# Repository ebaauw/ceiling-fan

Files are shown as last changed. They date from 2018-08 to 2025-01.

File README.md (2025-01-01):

# ceiling-fan

## Ceiling Fan control from deCONZ
Copyright © 2018-2025 Erik Baauw. All rights reserved.

This repository documents my efforts for controlling my dumb ceiling fans from [deCONZ](https://github.com/dresden-elektronik/deconz-rest-plugin), and, through [homebridge](https://github.com/nfarina/homebridge) and [homebridge-hue](https://github.com/ebaauw/homebridge-hue), from HomeKit.
As no-one seems to have done this before (see [deCONZ issue #717](https://github.com/dresden-elektronik/deconz-rest-plugin/issues/717)), I decided to try and hack together my own solution.

I have three regular ceiling fans.  Each fan has a single-phase 240V, 50Hz AC motor, and three GU.10 light spots.  As I've already installed smart lights, I'm only looking for a solution to smartify the control the fan speed, and possibly the direction.

The fan has four connection wires under the canopy: Motor Life (black), Lights Life (also black), Neutral (blue) and Ground (green/yellow).  My ceiling outlet only has three wires: Life (black, from the traditional wall switch) Neutral (blue), Earth (green/yellow), so the motor and lights are controlled by a single wall switch wire.  The smart lights prefer to be powered on always, so the wall switch is used only to cut power from the fan, not for regular control.  As I don't want to pull a new switched life wire, replacing the wall switch is not an option.

### ZigBee In-Wall Switch
My first attempt was to try and install a ZigBee in-wall switch in the fan's canopy, in between the incoming life wire and the motor life wire.  I mutilated an Xiaomi Aqara in-wall switch (`lumi.ctrl_ln2.aq1`), took off the front and cut off the edges supporting the keys, leaving a 6cm by 6cm by 3cm box, which fits the canopy.  After assembling the fan, it worked.  No speed control, but deCONZ was able to switch the fan on and off at speed preset by the pull-chain switch.

However, the Xiaomi switch broke while I was balancing the fan's blades (frequently switching on and off the fan using the Xiaomi switch).  The relays switch off automatically a second after switching on, or won't switch on at all.  Not sure if this is just my luck, or whether the switch doesn't like the fan starting up.  The fan is 50W, while the switch is rated for 2500W (10A).  Incidentally, one of my OSRAM Lightify smart plugs (the old model) exhibits the same symptoms.  It was powering a portable fan...

Before the switch broke, I already ordered two more Xiaomi switches.  They turned out to be the newer ones without a Neutral connection (they use a minute current on the one of the L1 or L2 wires to power the electronics).  That means they're powered off, when the pull-chain is in the off position.   Also, these are the end-device variants (`lumi.ctrl_neutral2`), now fully supported in deCONZ v2.05.37.  I mutilated the housing and installed them, fingers crossed.

#### Update after Several Months.
I got another `lumi.ctrl_ln2.aq1` switch for the third fan.  It worked for a couple of weeks, but now shows same defect as the first one.  It crashes every 60 to 70 seconds, sending a new device announcement and switching off the relays on subsequent startup.  The relays seem to work fine, the problem seems to be with the switch's power supply and/or firmware.  I haven't been able to isolate a particular ZigBee message that would cause the crash.  Also the crashes are too regular to be caused by irregularities in the mains power.  I double checked the first switch: it shows the same behaviour, but crashes even more frequently.

The two `lumi.ctrl_neutral2` switches still work.  I ordered a third one (I hope) to replace the broken switch.

### Speed Control
Even if the new switches won't break, it would be so much cooler also to be able to control the fan speed from HomeKit.  The in-wall smart dimmers I've seen are rated for lights only (and probably beyond my budget anyways).

With each pull on the chain, the fan speed cycles through _Off_, _High_, _Medium_, _Low_.  The pull-chain switch has a simple mechanical mechanism, that switches it's input to one of three output wires (presumably connected to different coil windings on the AC motor).  So, at least in theory, fan speed could be controlled by three switches, when making sure at most one output line is powered at a time.  Doing that in software seem risky, given the beta status of deCONZ and the hobby status of homebridge-hue, so I'd prefer a hardware solution.  Also, I haven't come across triple-gang in wall switches, so I'd need to use at least two.  No way two Xiaomi switches will fit, and two ubisys S2 switches per fan is beyond my budget.

The hardware solution would be based on chaining relays, connecting the NC (normally closed) output of one relay to the COM input of a second relay, and NO (normally open) output to the COM of a third relay.  This way, I can switch between four outputs: the second relay's NO and NC, and the third relay's NO and NC.  The second relay switches between _Off_ (NC) and _Low_ (NO), the third between _Medium_ (NC) and _High_ (NO), while the first relay switches between the second (NC) and third (NO) relays.

RL1 | RL2 | RL3 | NC 2 | NO 2 | NC 3 | NC 3 | Speed
----| --- | --- | ---- | ---- | ---- | ----- | -----
off | off | off | power | | (no input) | | _Off_
off | off | on* | power | | | (no input) | _Off_
off | on  | off | | power | (no input) | | _Low_
off | on  | on* | | power | | (no input) | _Low_
on  | off | off | (no input) | | power | | _Medium_
on  | off | on  | (no input) | | | power | _High_
on  | on* | off | | (no input) | power | | _Medium_
on  | on* | on  | | (no input) | | power | _High_

\*) Since there's no power on the input, best leave the relay off.

While I would still occasionally need to switch two relays for a single transition (e.g. from _Off_ to _High_), only one output is connected to the life wire at all times.

### First Proof of Concept
Before messing with 240V, I figured I'd better create a low-voltage proof of concept.
I got myself an [Ardino Starter Kit](https://www.arduino.cc/en/Main/ArduinoStarterKit) and a [Seeed Relay Shield v3](http://wiki.seeedstudio.com/Relay_Shield_v3/), with four relays.  This still leaves a fourth relay available for direction control.

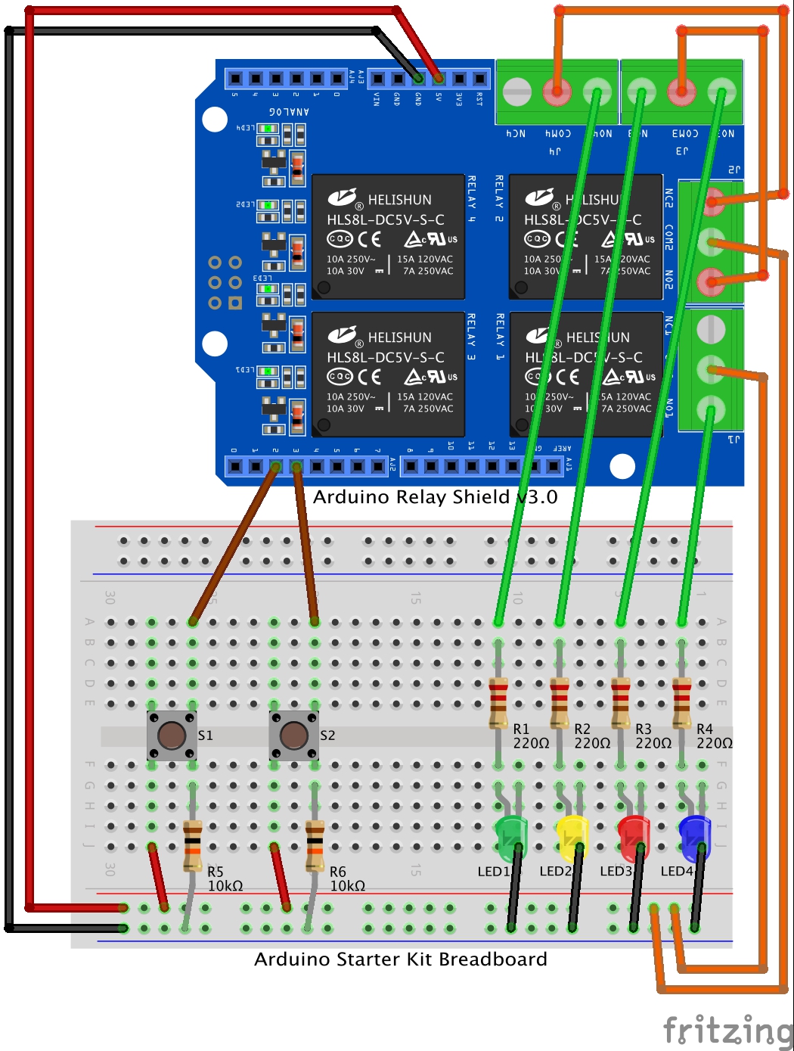
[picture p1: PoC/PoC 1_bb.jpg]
To test the logic, I build the following prototype: 

While the relays themselves should be able to switch 240V AC up to 10A, I'm pretty sure that this will blow up the board (and probably the Arduino).  In this prototype I use the relays to switch 5V DC from the Arduino.  Not something you'd normally need a relay for, but fine for testing the logic.  Relay 1 is simulating the fan's direction, switching between _Down_ (NC) and _Up_ (NO, blue LED).  Relays 2 to 4 are used for the fan speed: relay 2 switches between relays 4 (NC) and 3 (NO); relay 4 switches between _Off_ (NC) and _Low_ (NO, green LED); relay 3 switches between _Medium_ (NC, yellow led) and _High_ (NO, red led).  The switches are used to simulate the pull-chain switches: S1 for pulling the speed switch and S2 for changing the direction switch.  I programmed the Arduino with the following [sketch](https://github.com/ebaauw/ceiling-fan/blob/master/PoC/PoC.ino).

This works as intended.  Next step will be figuring out the radio logic.

### MHCOZY 4-Channel Zigbee Relay
I finally found an AC-powered, 4-channel Zigbee relay with NO and NC outputs per channel: the [MHCOZY](https://www.amazon.nl/dp/B0C9Y5LTFJ/ref=pe_28126711_487102941_TE_SCE_dp_1).
According to its specs, the relays can be used to drive motors, so they should be happy with the fan's inductive load.
The downsides: it's quite large, 8 x 8 x 3cm, and it's Tuya.

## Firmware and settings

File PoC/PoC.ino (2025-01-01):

// PoC.ino
// Copyright © 2018-2025 Erik Baauw. All rights reserved.
//
// First proof of concept for ceiling fan controller.

// Arduino Relay Shield v3.0 PIN assignments.
#define RELAY1       7
#define RELAY2       6
#define RELAY3       5
#define RELAY4       4
#define ONBOARD_LED 13

// ***** Wiring ****************************************************************

#define RELAY_OFF_LOW     RELAY4    // NC: off            NO: low speed
#define RELAY_MEDIUM_HIGH RELAY3    // NC: medium speed   NO: high speed
#define RELAY_POWER       RELAY2    // NC: RELAY_OFF_LOW  NO: RELAY_MEDIUM_HIGH
#define RELAY_DIRECTION   RELAY1    // NC: down           NO: up
#define BUTTON_SPEED      2
#define BUTTON_DIRECTION  3

// ***** Fan speed control *****************************************************

#define OFF 0
#define LOW_SPEED 1
#define MEDIUM_SPEED 2
#define HIGH_SPEED 3

void setSpeed(int speed) {
  switch (speed) {
    case OFF:
      Serial.print("off\n");
      digitalWrite(RELAY_OFF_LOW, LOW);       // off
      digitalWrite(RELAY_POWER, LOW);         // power RELAY_OFF_LOW
      digitalWrite(RELAY_MEDIUM_HIGH, LOW);   // not powered
      break;
    case LOW_SPEED:
      Serial.print("low speed\n");
      digitalWrite(RELAY_OFF_LOW, HIGH);      // low speed
      digitalWrite(RELAY_POWER, LOW);         // power RELAY_OFF_LOW
      digitalWrite(RELAY_MEDIUM_HIGH, LOW);   // not powered
      break;
    case MEDIUM_SPEED:
      Serial.print("medium speed\n");
      digitalWrite(RELAY_MEDIUM_HIGH, LOW);   // medium speed
      digitalWrite(RELAY_POWER, HIGH);        // power RELAY_MEDIUM_HIGH
      digitalWrite(RELAY_OFF_LOW, LOW);       // not powered
      break;
    case HIGH_SPEED:
      Serial.print("high speed\n");
      digitalWrite(RELAY_MEDIUM_HIGH, HIGH);  // high speed
      digitalWrite(RELAY_POWER, HIGH);        // power RELAY_MEDIUM_HIGH
      digitalWrite(RELAY_OFF_LOW, LOW);       // not powered
      break;
  }
}

void setupSpeed() {
  pinMode(RELAY_OFF_LOW, OUTPUT);
  pinMode(RELAY_MEDIUM_HIGH, OUTPUT);
  pinMode(RELAY_POWER, OUTPUT);
}

// ***** Fan direction control *************************************************

#define DOWN 0
#define UP 1

void setDirection(int direction) {
  switch (direction) {
    case DOWN:
      Serial.print("blowing down\n");
      digitalWrite(RELAY_DIRECTION, LOW);     // down
      break;
    case UP:
      Serial.print("blowing up\n");
      digitalWrite(RELAY_DIRECTION, HIGH);    // up
      break;
  }
}

void setupDirection() {
  pinMode(RELAY_DIRECTION, OUTPUT);
}

// ***** Button handler ******************************************************

#define NONE    0
#define PRESS   1
#define RELEASE 2

bool buttonReleased[32];

void setupButton(int button) {
  pinMode(button, INPUT);
  buttonReleased[button] = true;
}

int buttonEvent(int button) {
  if (digitalRead(button) == HIGH) {
    if (buttonReleased[button]) {
      buttonReleased[button] = false;
      Serial.print("button pressed\n");
      return PRESS;
    }
  } else if (!buttonReleased[button]) {
    buttonReleased[button] = true;
    Serial.print("button released\n");
    return RELEASE;
  }
  return NONE;
}

// ***** Main Program ********************************************************

int speed = OFF;
int direction = DOWN;
int buttonSpeedReleased = true;
int buttonDirectionReleased = true;

void setup() {
  Serial.begin(9600);
  Serial.print("Ceiling fan PoC\n");
  setupSpeed();
  setupDirection();
  setupButton(BUTTON_SPEED);
  setupButton(BUTTON_DIRECTION);
  pinMode(ONBOARD_LED, OUTPUT);
}

void loop() {
  if (buttonEvent(BUTTON_SPEED) == PRESS) {
    speed += 3;
    speed %= 4;
    setSpeed(speed);
  }
  if (buttonEvent(BUTTON_DIRECTION) == PRESS) {
    direction = 1 - direction;
    setDirection(direction);
  }
}
